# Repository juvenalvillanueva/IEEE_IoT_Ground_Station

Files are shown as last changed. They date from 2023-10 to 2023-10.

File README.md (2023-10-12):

# An IoT Ground Station: Mechanics, Control, Antenna, and Reception from a LoRa SatelliteNetwork

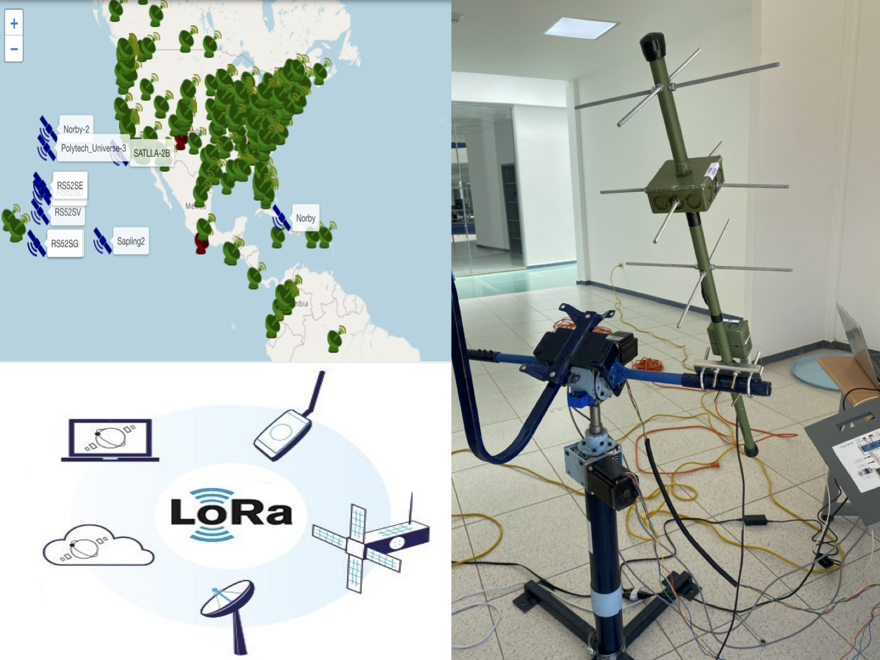
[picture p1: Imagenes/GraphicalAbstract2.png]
Graphical abstract


Se presentan los recursos y la documentación adicional obtenidos como resultado por el desarrollo del manuscrito "An IoT Ground Station: Mechanics, Control, Antenna, and Reception from a LoRa Satellite Network" publicado en IEEE Latin America Transactions. Esta información se organiza en tres carpetas: 

1. Antena, donde podrá observar los archivos del diseño y simulación de este dispositivo.

   a) El archivo Turstile.s1p es un archivo generado por un analizador vectorial redes (VNA) que contiene el parámetro S de 1 puerto (S11) medido en el laboratorio.
   
   b) El archivo turstile.nec es un archivo generado en el software libre 4NEC2 para simulación de la antena. El software puede ser descargado en:https://www.qsl.net/4nec2/.
   
2. Sistema Mecánico, aquí se encuentran los archivos de diseño y los planos para poder fabricar cada una de las piezas que conforman al sistema mecánico.
3. PID, en esta carpeta se encuentra  el código de programación del controlador PID discreto utilizado para manipular las articulaciones. Para ello, se utilizó la plataforma de Arduinoal debido a que se utilizó una placa de esta marca.

## Requerimientos
 
- Sistema operativo Windows.
- Microsoft Excel.
- Matlab 2018 o posteriores con el “RF Toolbox” instalado.
- Última versión de 4NEC2.
- SolidWorks 2018 o posteriores.
- Plataforma de Arduino.

## Imagenes

<div id="header" align="center">
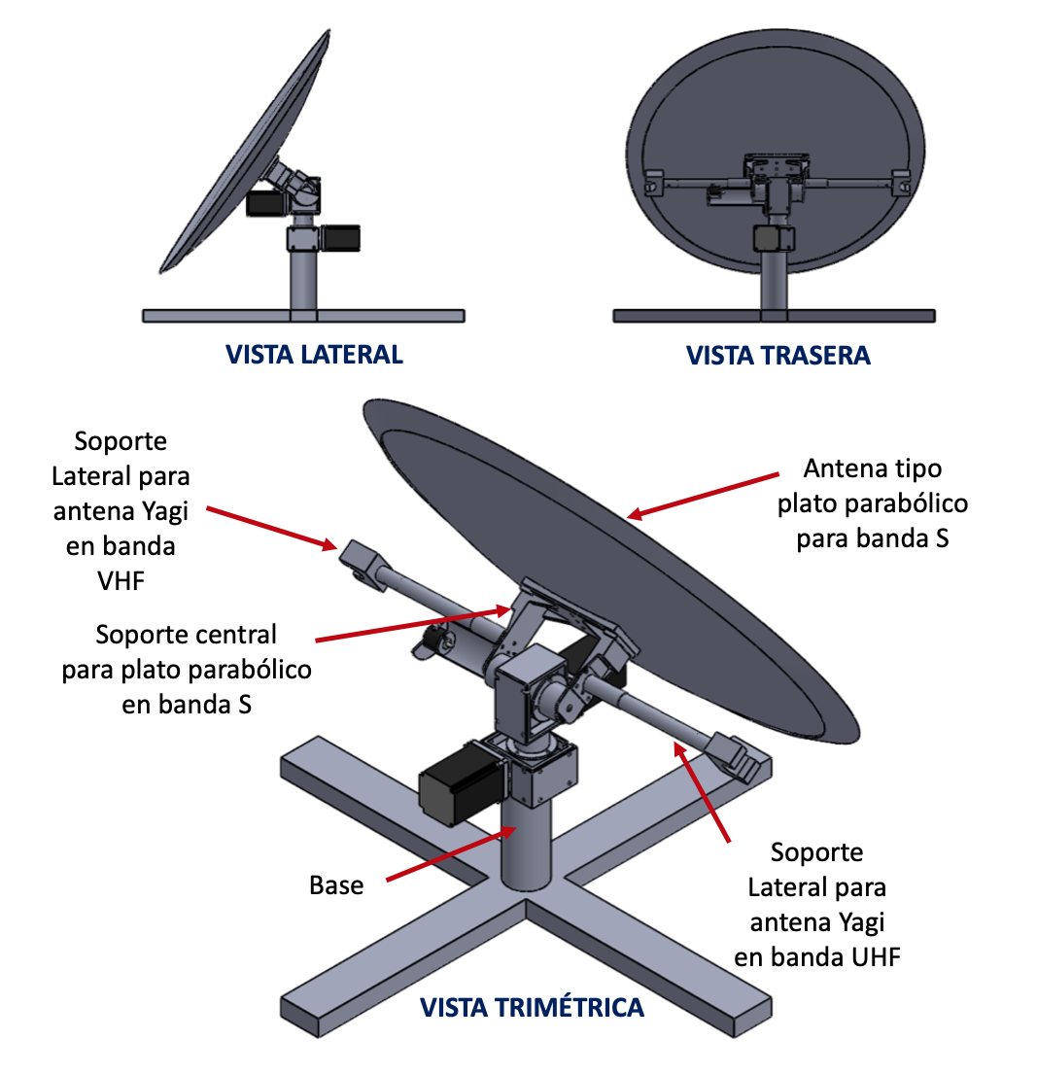
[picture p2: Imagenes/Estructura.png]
  
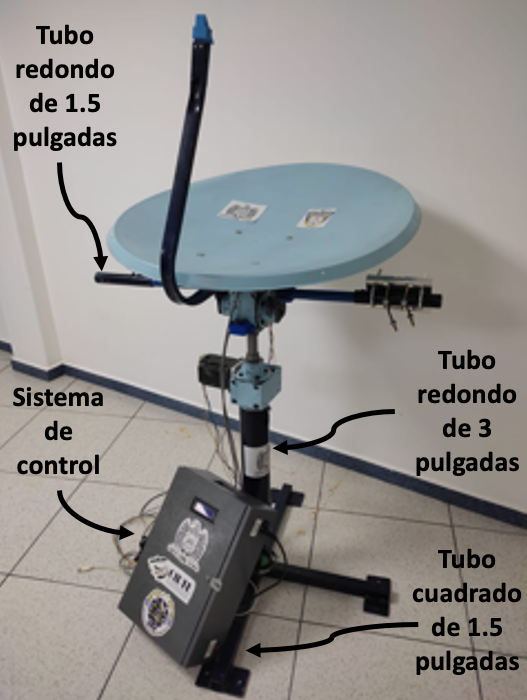
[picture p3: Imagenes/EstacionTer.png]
  
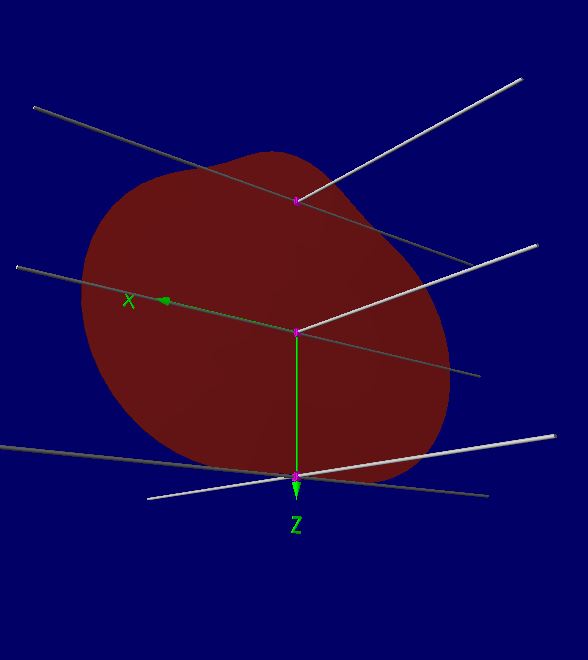
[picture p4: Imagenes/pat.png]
  
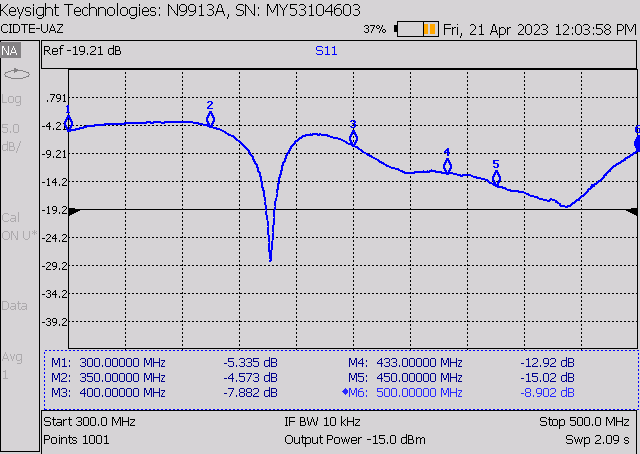
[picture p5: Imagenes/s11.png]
  
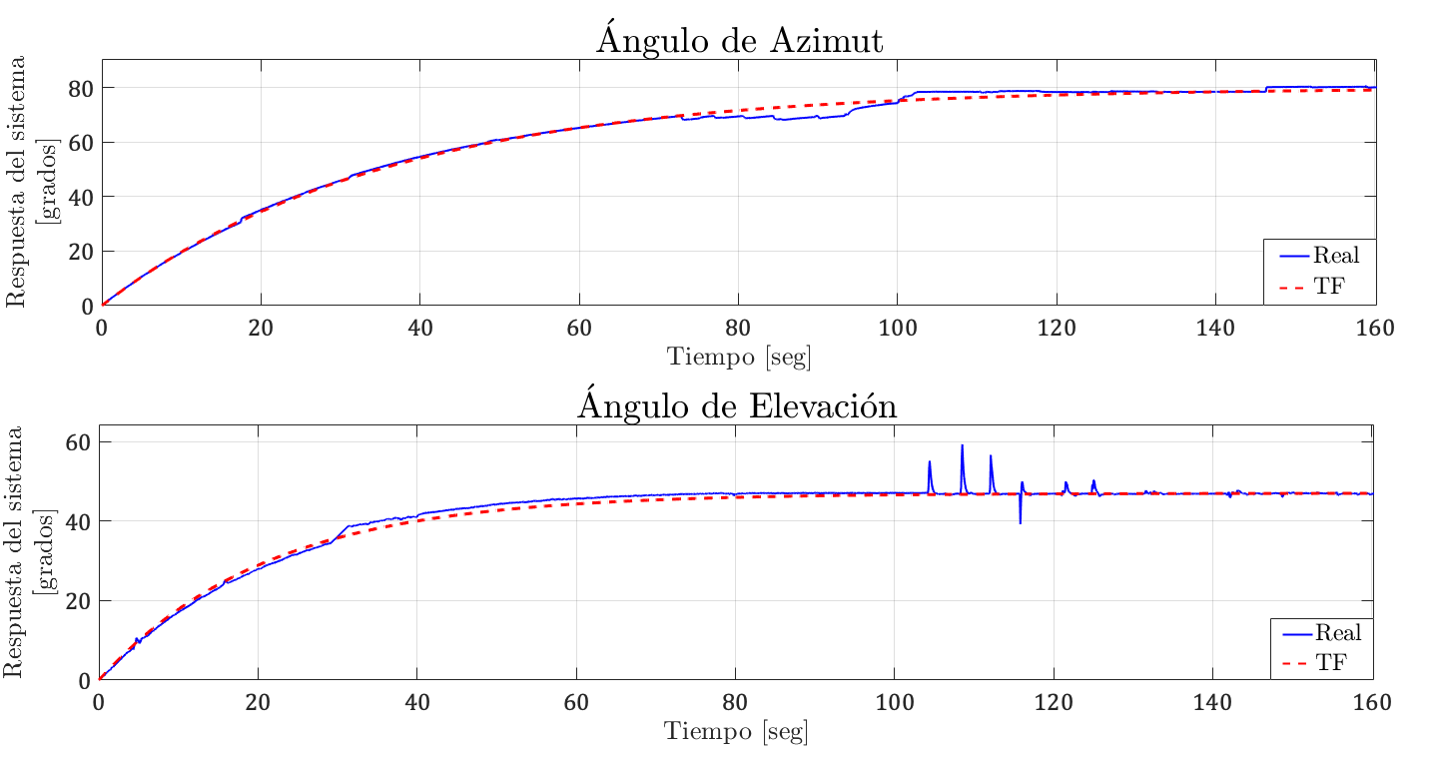
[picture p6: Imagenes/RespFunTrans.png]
 
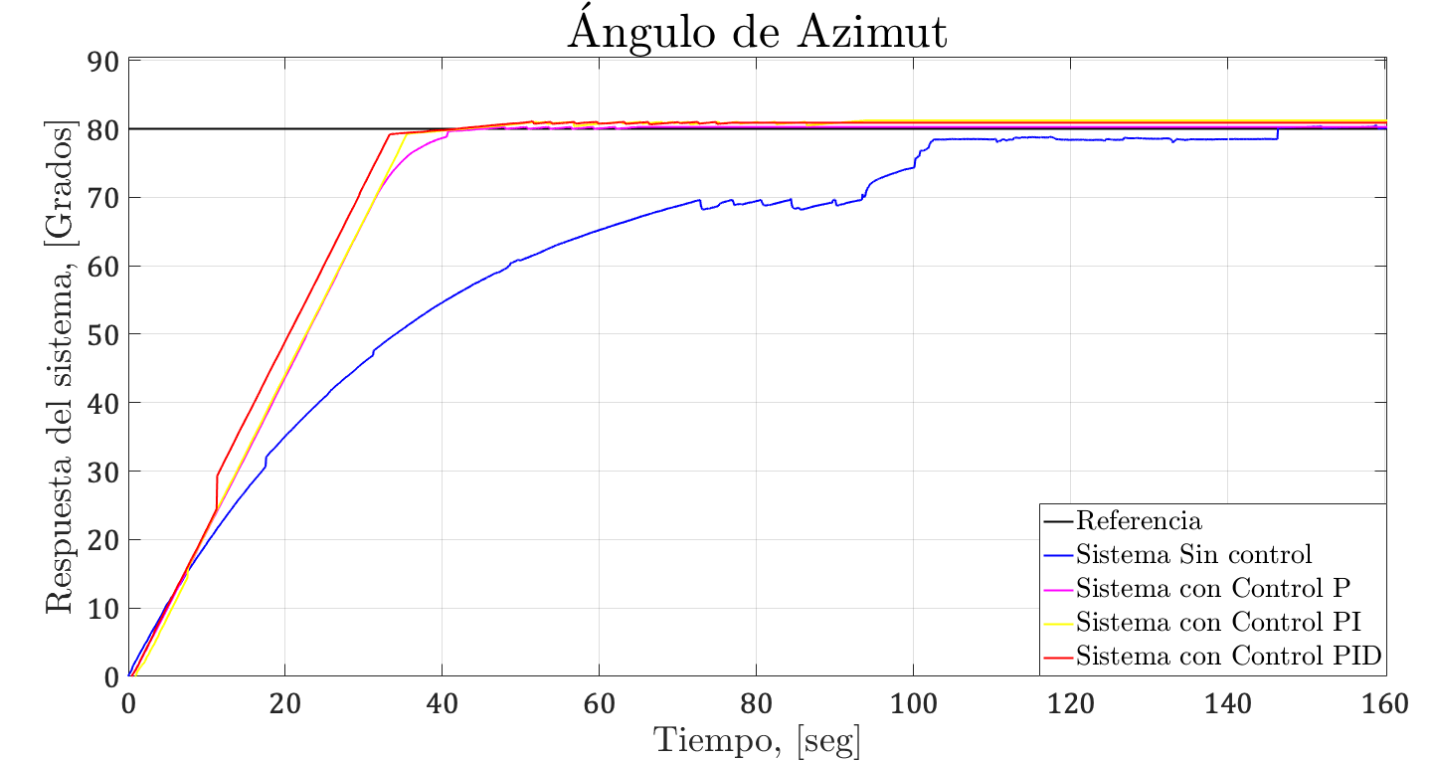
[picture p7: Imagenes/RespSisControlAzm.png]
  
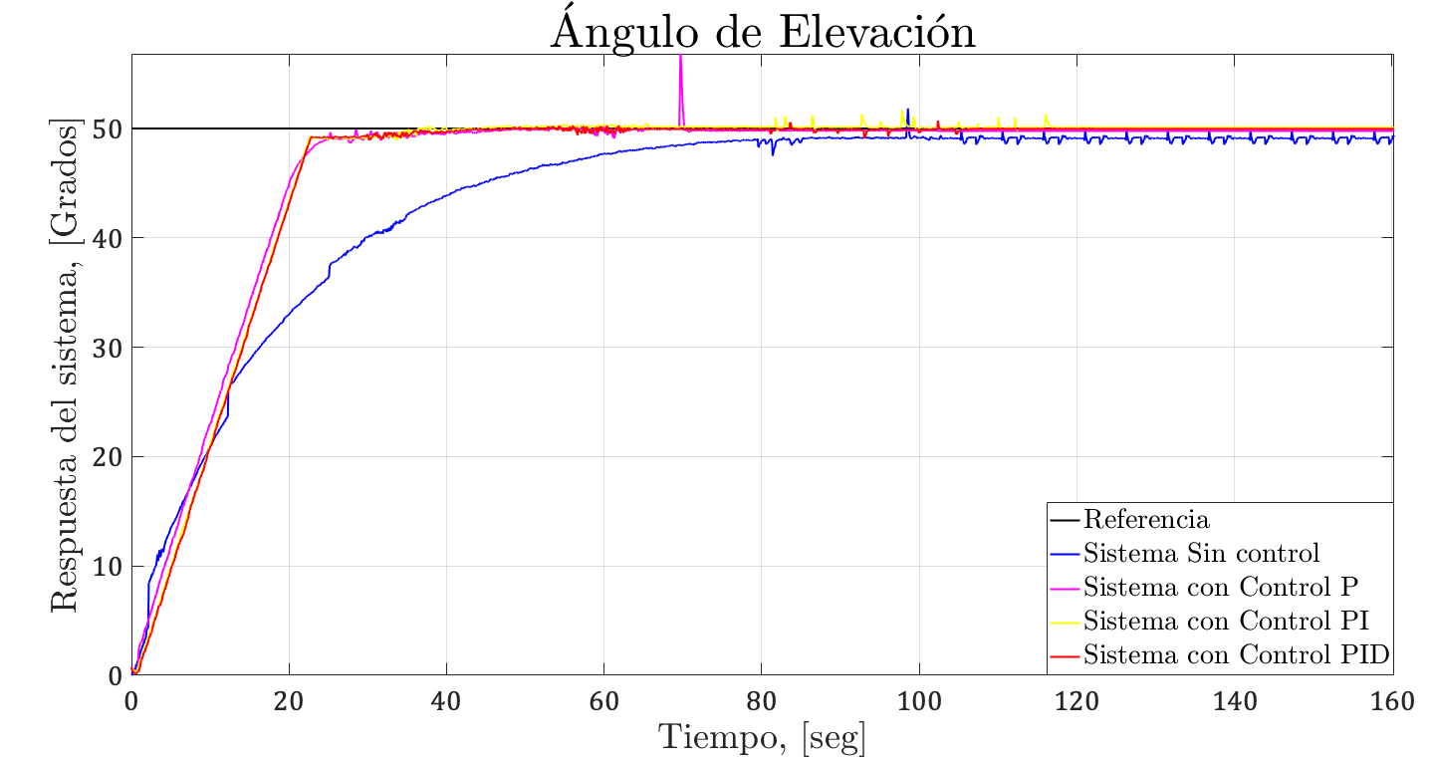
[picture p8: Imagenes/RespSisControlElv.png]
  
</div>

## Instrucciones

1.a) Las mediciones incluidas en el archivo Turstile.s1p pueden ser visualizadas con solo arrástralo a una nueva hoja de Excel. Ya en Excel se pueden observar tres columnas correspondientes al barrido de frecuencia, la magnitud del parámetro S11 (coeficiente de reflexión en dB) y su fase. Con ello se pueden obtener graficas tanto de magnitud y fase de S11 vs frecuencia. Las mediciones contenidas en el archivo archivo puede ser también observadas en alguna reciente versión de Matlab con el de “RF Toolbox” instalado. Se escribe un m-file en el “Editor” para graficar el parámetro S11 en dB de la siguiente forma:

S=sparameters(“Turnstile.s1p”);
rfplot(S)

Si desean graficar otros parámetros de la antena como carta de Smith, VWR o impedancia, cheque la ayuda con en la ventana “Comand Window” tecleando:

help rfplot

1.b) El archivo turstile.nec se abre en la venta “Main” en la opción “Open 4NEC2 in/out file”. Este archivo ya hecho a modo para la antena utilizada permite observar los parámetros de antena simulados como los dependientes de la frecuencia como S11 en dB, VWR, impedancia, etc. Para más información del uso de 4NEC2, vea los siguientes videos en YouTube:

- https://www.youtube.com/watch?v=vaLx3_F6-b4
- https://www.youtube.com/watch?v=T5hyCiytaFk

2. Se comparten los archivos de los planos en formato PDF de manera que puedan utilizarlos para fabricar y reproducir cada una de las piezas mecánicas. Así también, los archivos en formato SLDPRT los cuales pueden abrir mediante SOLIDWORKS para que puedan realizar los cambios en el diseño conforme a sus requerimientos.
3. Para el control de las articulaciones, se utilizó una tarjeta de tipo ARDUINO, por lo que, el archivo del código del controlador PID esta en etse formato.

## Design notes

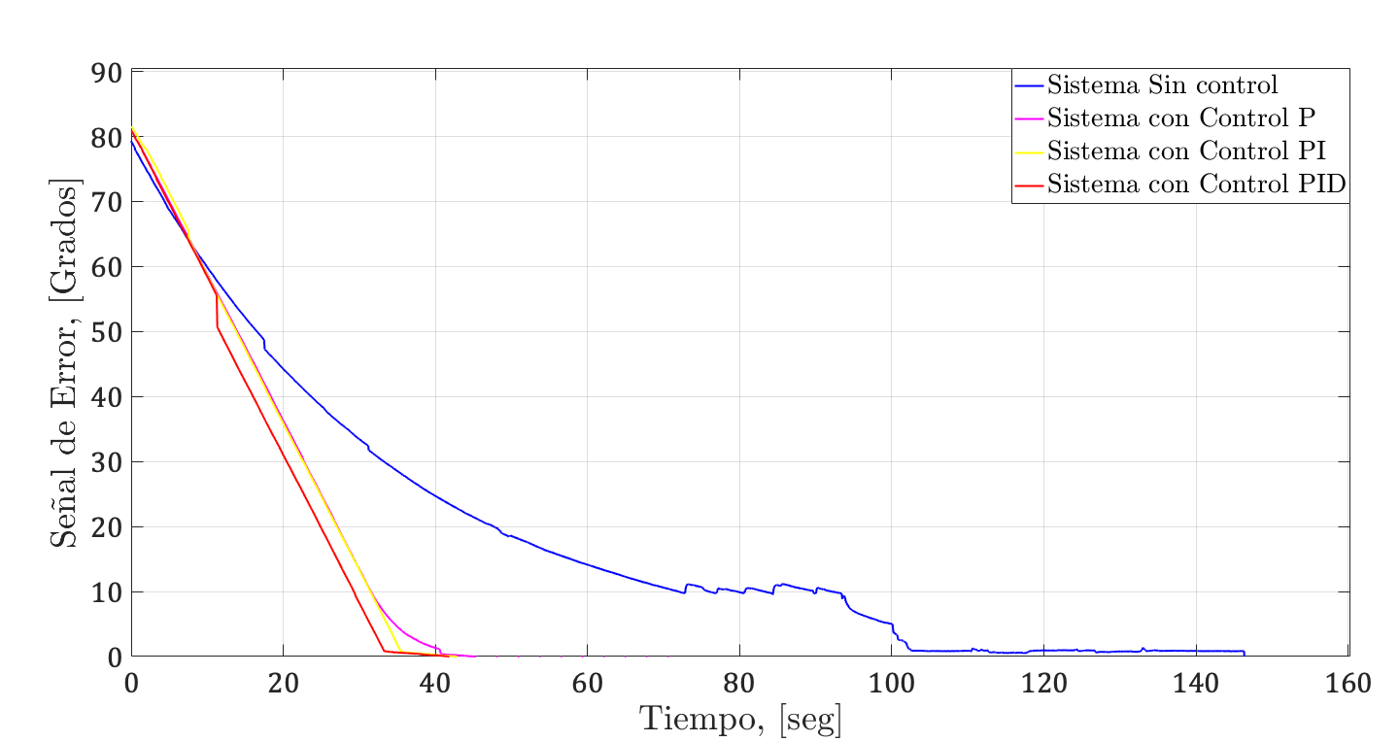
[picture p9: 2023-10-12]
Imagenes/E(t)Azm.png

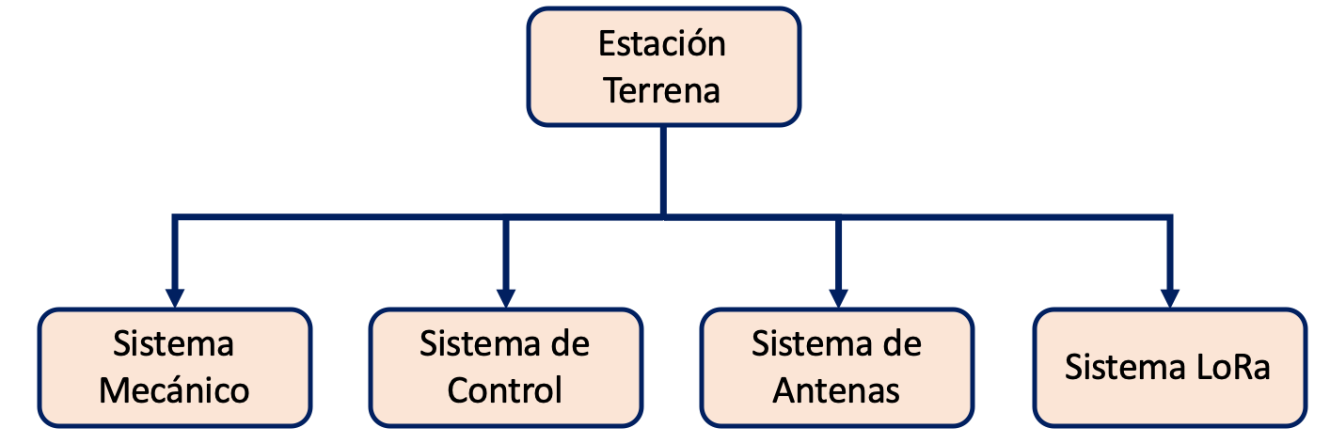
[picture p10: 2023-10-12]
Imagenes/Metodologia.png

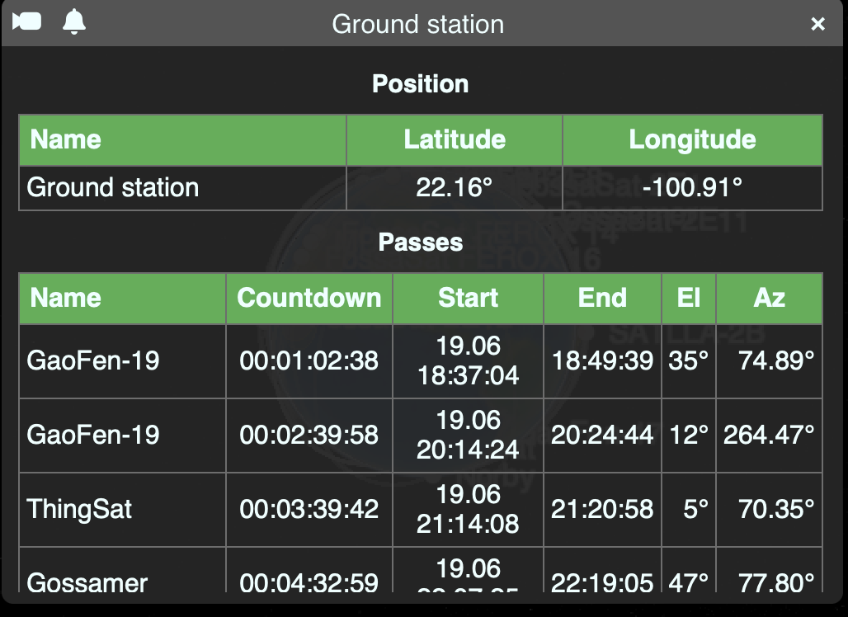
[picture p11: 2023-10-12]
Imagenes/coordenadas.png

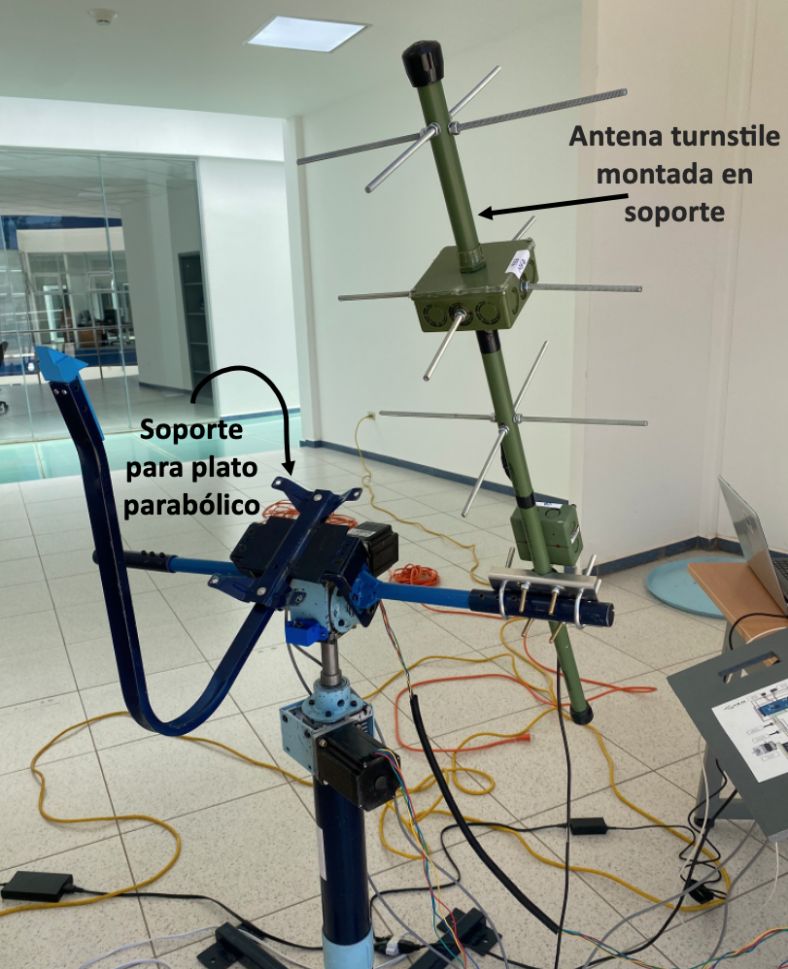
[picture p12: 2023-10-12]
Imagenes/antena.png

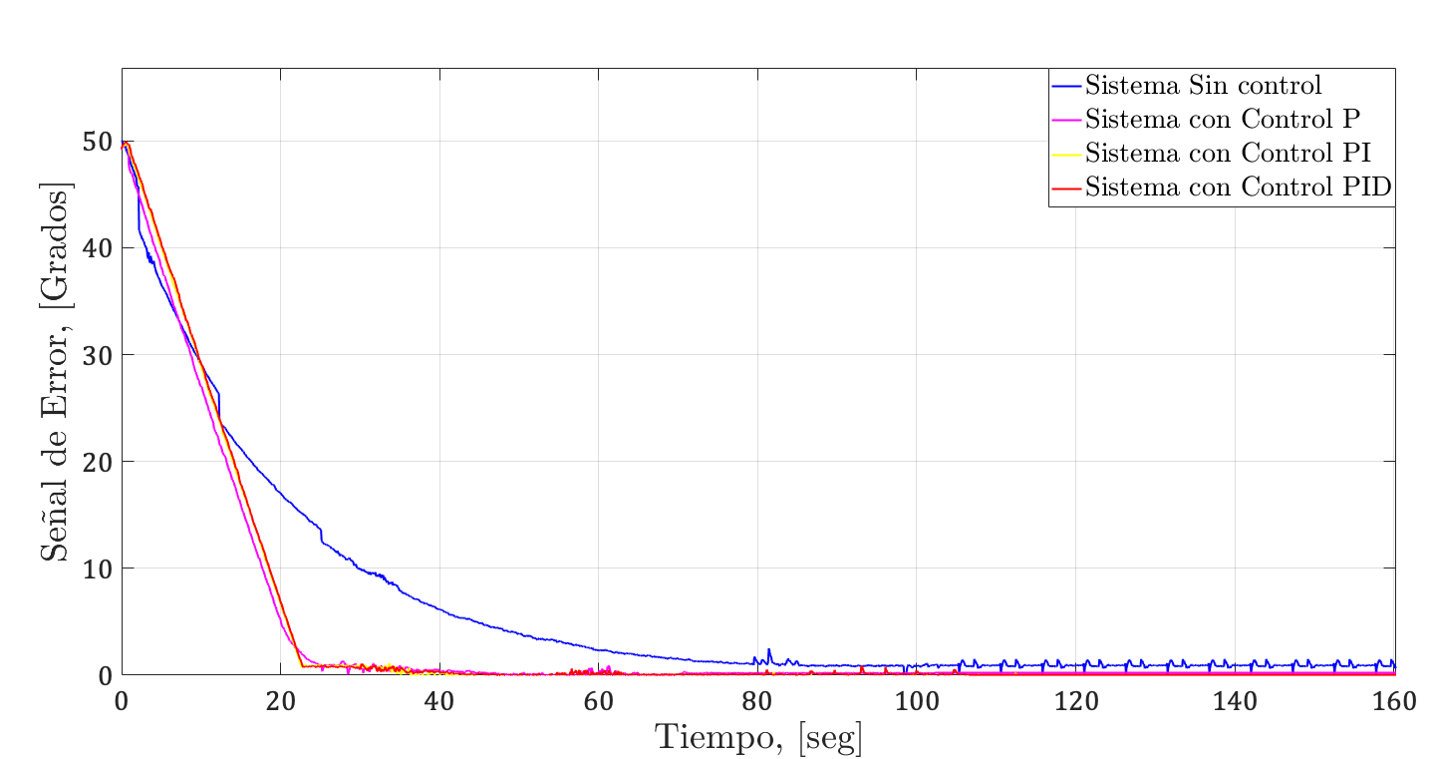
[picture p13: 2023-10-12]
Imagenes/E(t)Elv.png

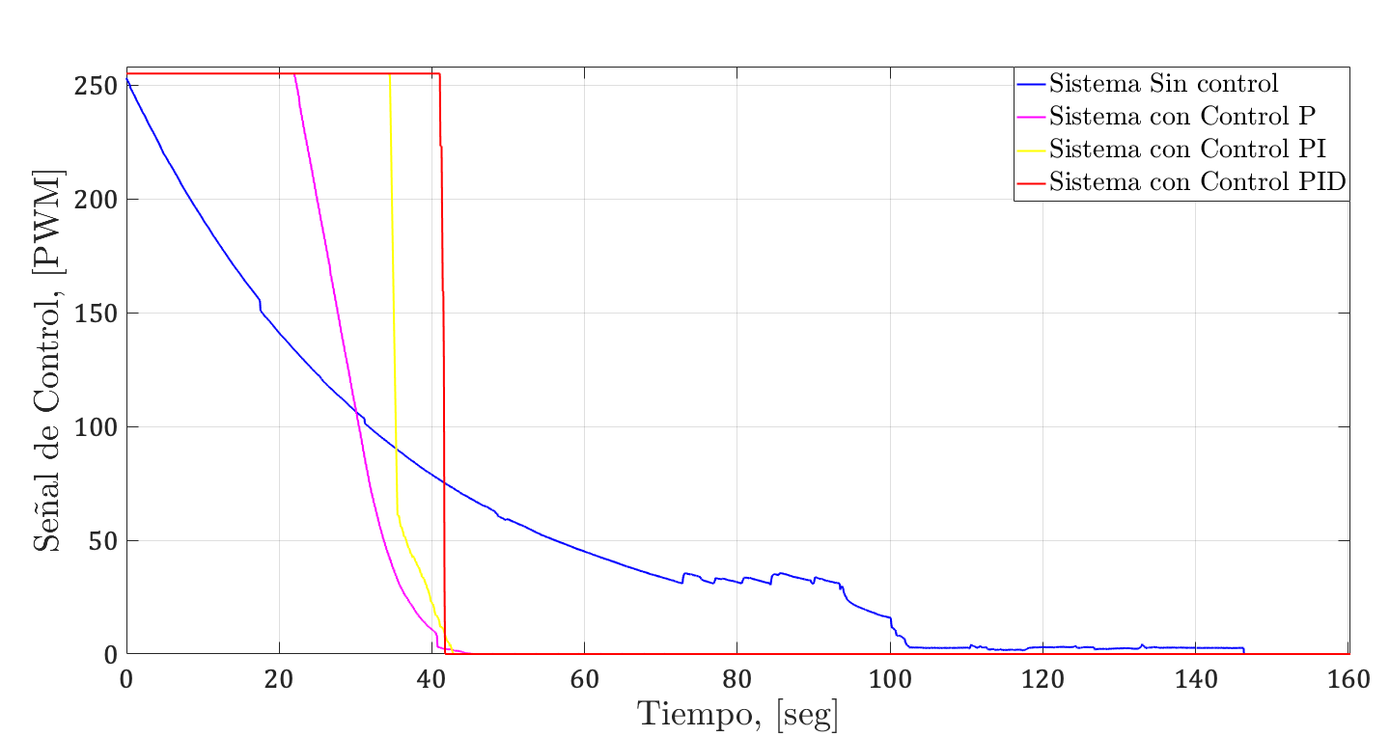
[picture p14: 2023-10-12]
Imagenes/U(t)Azm.png

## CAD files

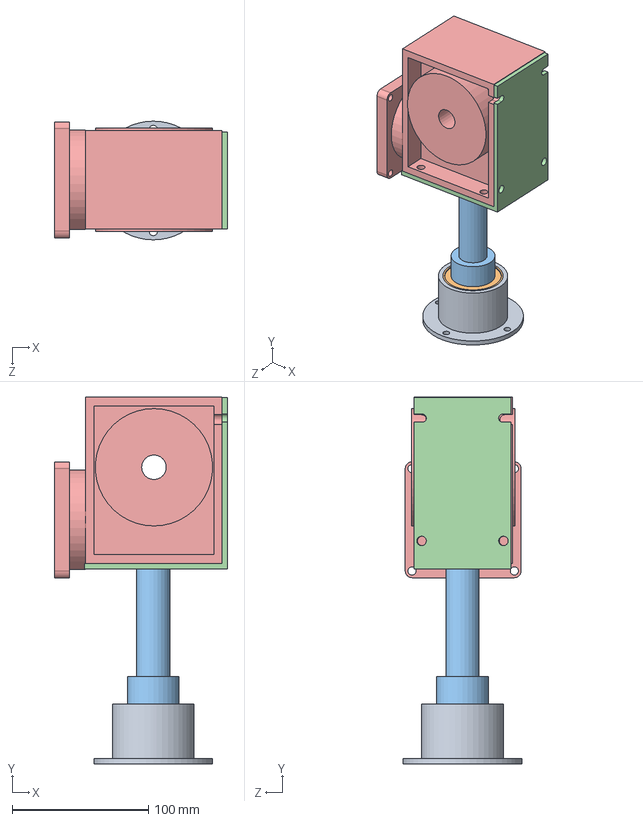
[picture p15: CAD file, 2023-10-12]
Sistema_Mecánico/Diseño/Ensamblaje_4_SoporteBrocheNMRV40.SLDASM
127.0 x 269.0 x 87.0 mm
Pieza_5_SoporteEjeReductor_NMRV40
Pieza_6_Balero52mm
Pieza_7_BrocheEje_NMRV40
Pieza_4_SoporteReductor_NMRV40
Pieza_1_Reductor_NMRV40

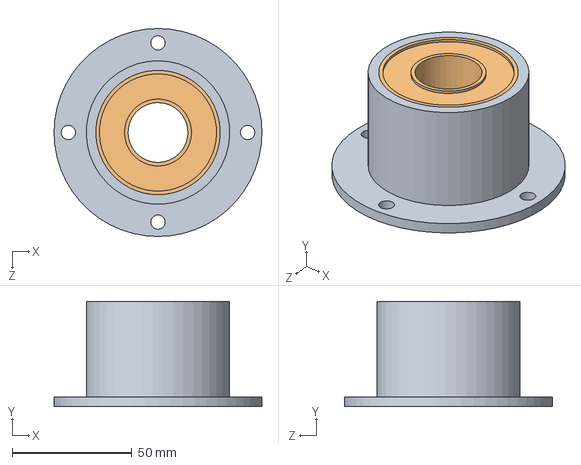
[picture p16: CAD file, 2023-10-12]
Sistema_Mecánico/Diseño/Ensamblaje_2_SoporteNMRV40_Balero52mm.SLDASM
87.0 x 44.0 x 87.0 mm
Pieza_5_SoporteEjeReductor_NMRV40
Pieza_6_Balero52mm

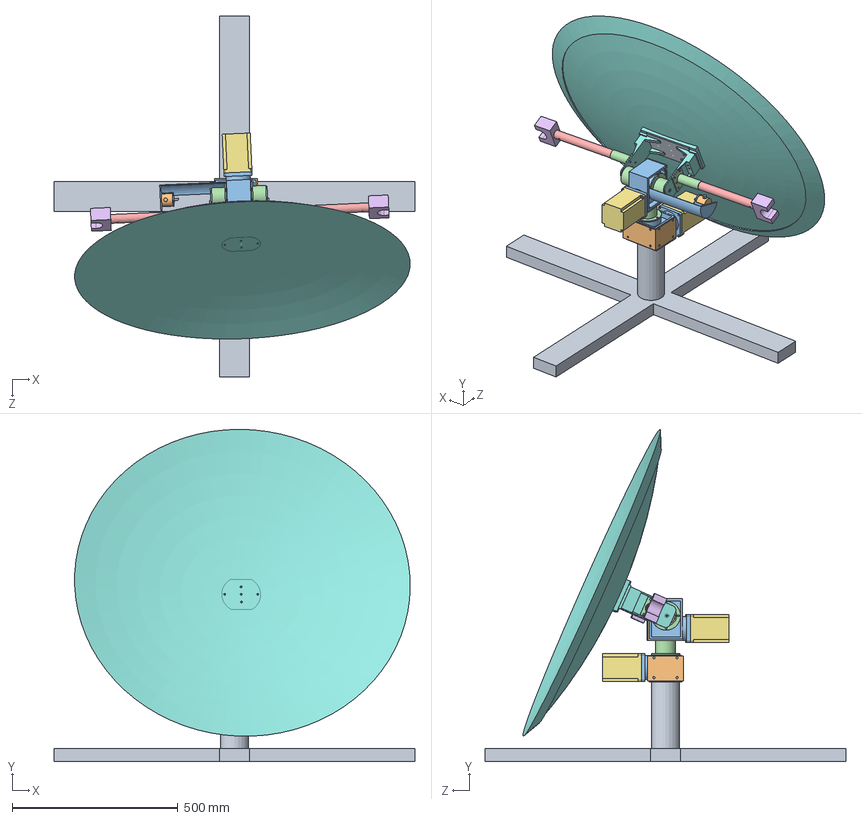
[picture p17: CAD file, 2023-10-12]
Sistema_Mecánico/Diseño/Ensamblaje_5_EstacionTerrena.SLDASM
1090.0 x 1003.2 x 1090.0 mm
Pieza_2_Base
Pieza_12_CajaReductorNMRV40
Pieza_1_Reductor_NMRV40 x 2
Pieza_5_SoporteEjeReductor_NMRV40 x 3
Pieza_6_Balero52mm x 3
Pieza_7_BrocheEje_NMRV40
Pieza_4_SoporteReductor_NMRV40
Pieza_8_SoporteBase x 2
Pieza_9_PlacaBase
Pieza_13_Encoder x 2
Pieza_5_SoporteEjeReductor_NMRV40_v2
Pieza_14 x 2
Pieza_15_BrazoAntena x 2
Pieza_16_BrocheAntena x 2
Pieza_17_MotorHB x 2
Pieza_20_Antena

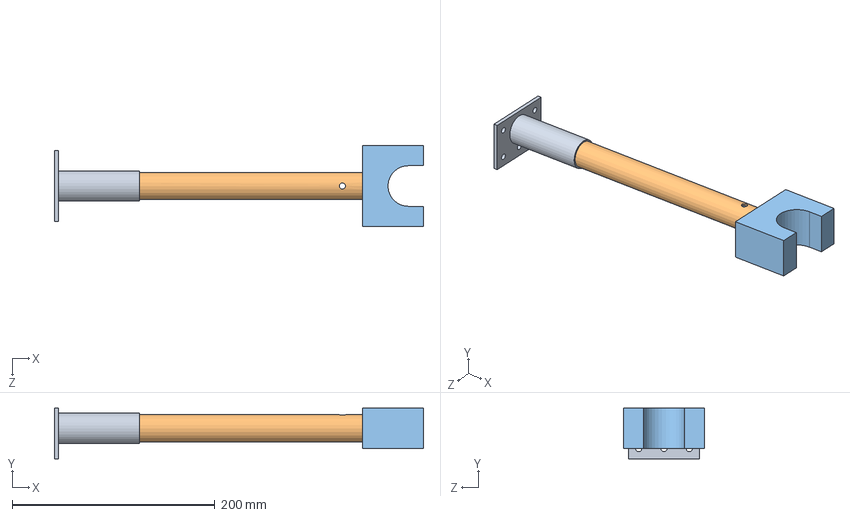
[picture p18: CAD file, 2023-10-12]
Sistema_Mecánico/Diseño/Ensamblaje_6_BrazoEstacion.SLDASM
364.0 x 50.0 x 80.0 mm
Pieza_14
Pieza_15_BrazoAntena
Pieza_16_BrocheAntena

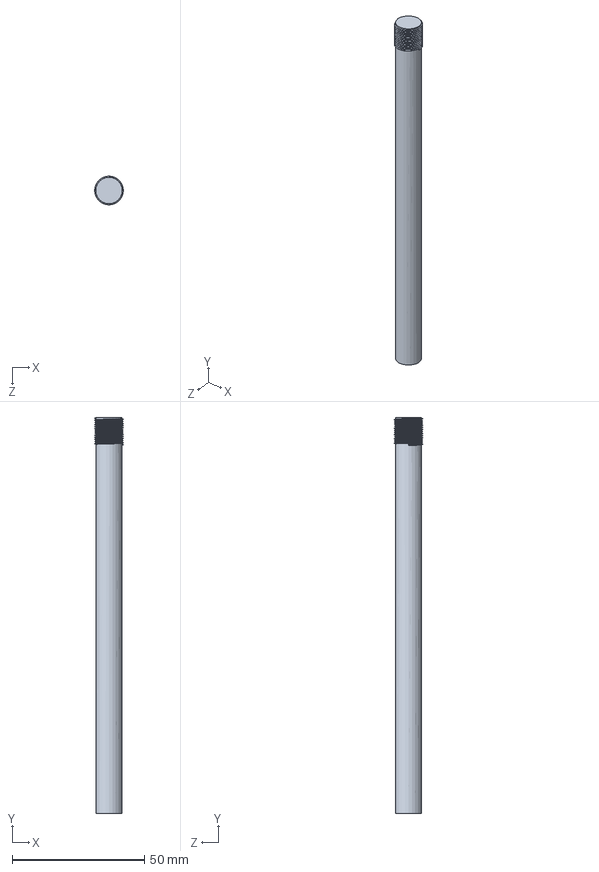
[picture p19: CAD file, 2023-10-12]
Sistema_Mecánico/Diseño/Pieza_11_EjeConectorEncoder.SLDPRT
10.9 x 150.0 x 10.9 mm

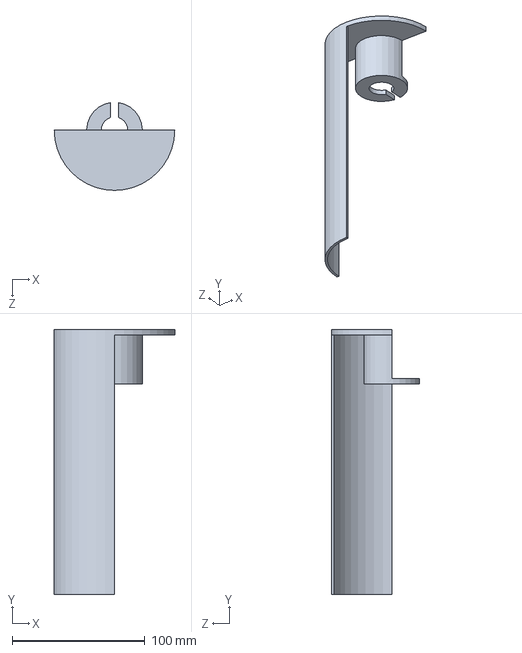
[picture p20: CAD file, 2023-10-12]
Sistema_Mecánico/Diseño/Pieza_5_SoporteEjeReductor_NMRV40_v2.SLDPRT
91.0 x 200.0 x 66.3 mm

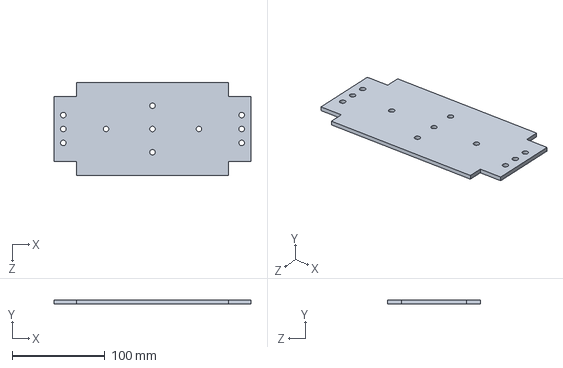
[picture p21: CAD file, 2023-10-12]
Sistema_Mecánico/Diseño/Pieza_9_PlacaBase.SLDPRT
212.0 x 4.00 x 100.0 mm

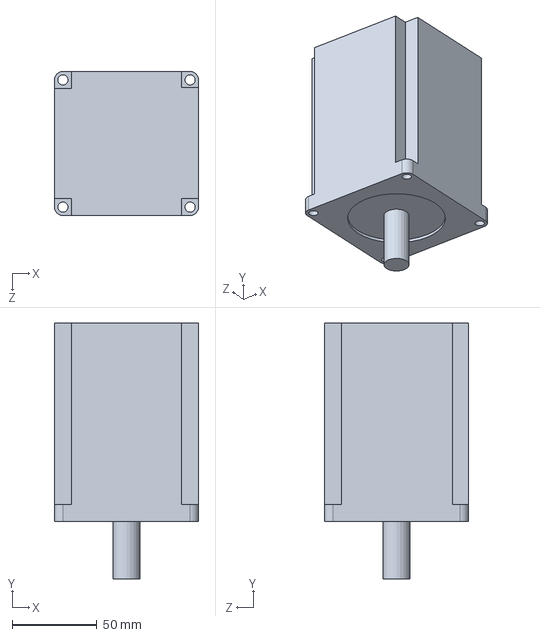
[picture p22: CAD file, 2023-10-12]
Sistema_Mecánico/Diseño/Pieza_17_MotorHB.SLDPRT
85.0 x 151.0 x 85.0 mm

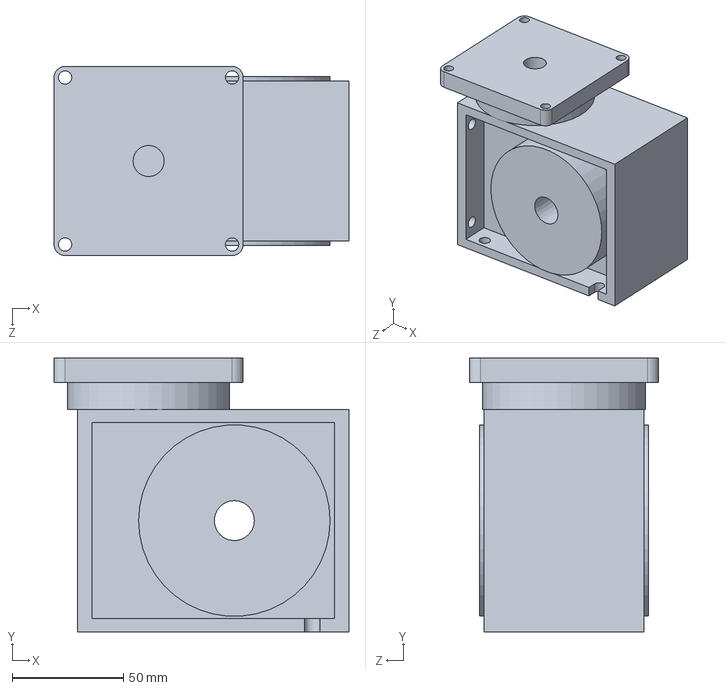
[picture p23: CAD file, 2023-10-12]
Sistema_Mecánico/Diseño/Pieza_1_Reductor_NMRV40.SLDPRT
132.5 x 123.0 x 85.0 mm

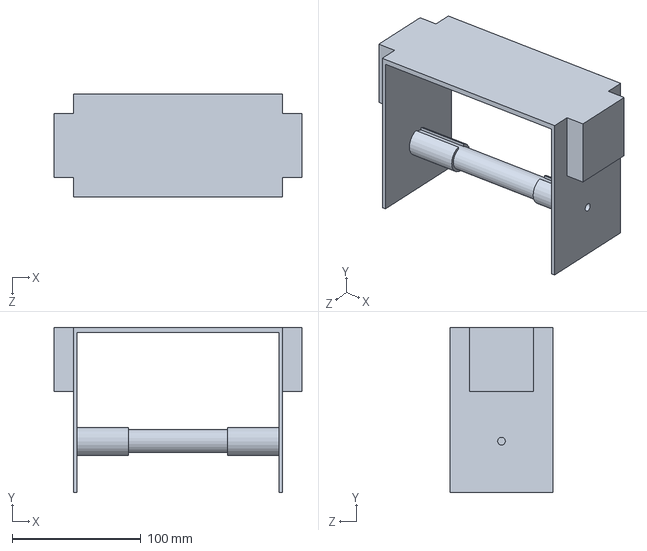
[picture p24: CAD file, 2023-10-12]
Sistema_Mecánico/Diseño/Pieza_3_SoporteAntena.SLDPRT
193.0 x 128.5 x 80.0 mm

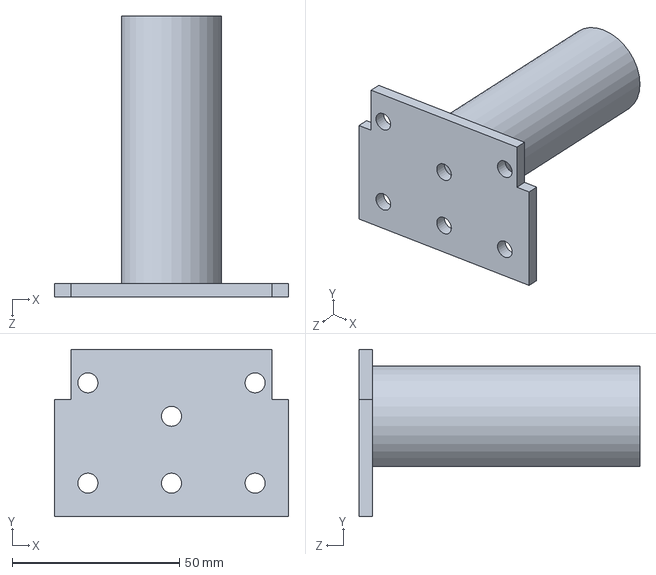
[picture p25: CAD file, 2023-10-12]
Sistema_Mecánico/Diseño/Pieza_14.SLDPRT
70.0 x 50.0 x 84.0 mm

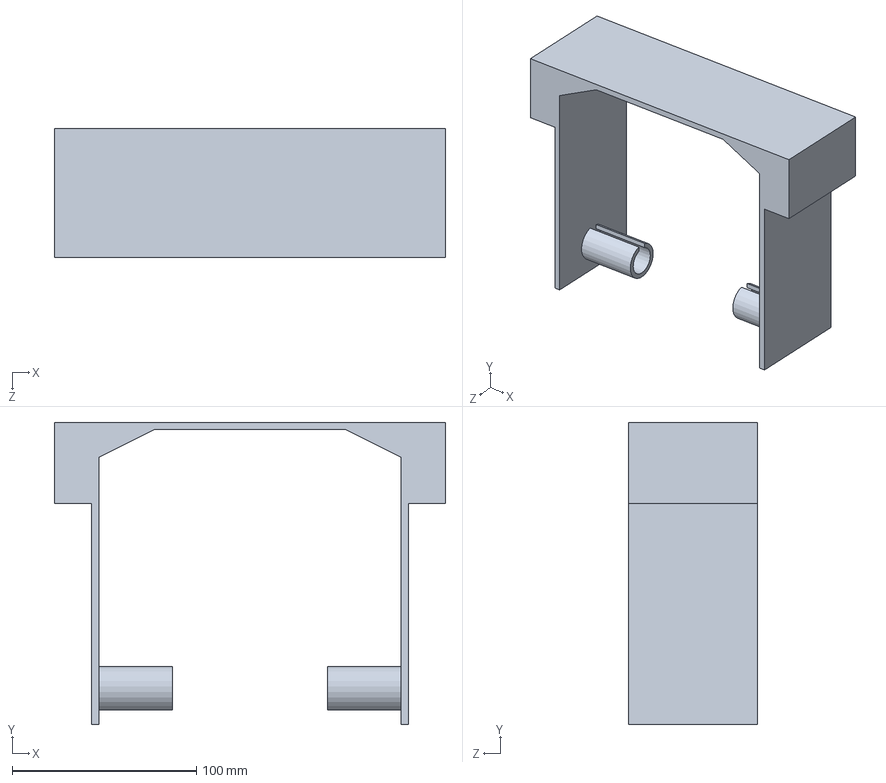
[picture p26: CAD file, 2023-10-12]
Sistema_Mecánico/Diseño/Pieza_10_SoporteAntena_V2.SLDPRT
212.0 x 164.0 x 70.0 mm

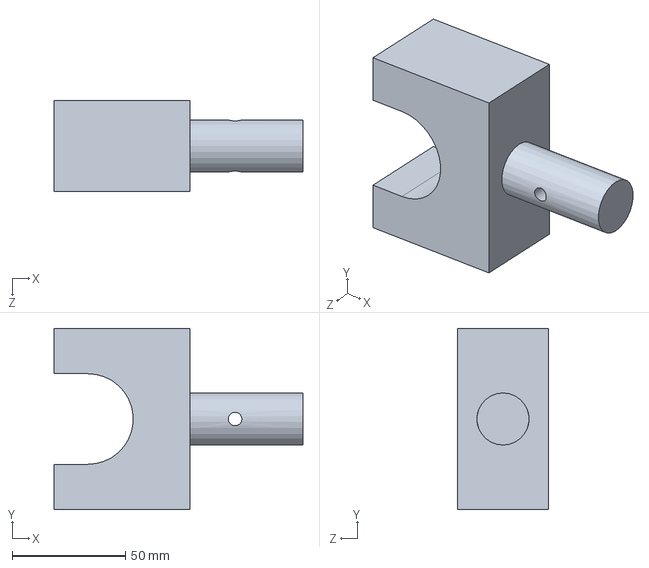
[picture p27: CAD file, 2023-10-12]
Sistema_Mecánico/Diseño/Pieza_16_BrocheAntena.SLDPRT
110.0 x 80.0 x 40.0 mm

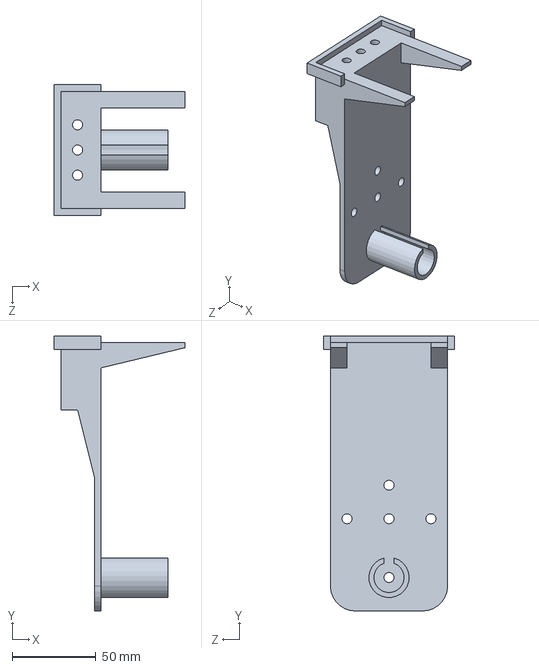
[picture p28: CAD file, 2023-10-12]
Sistema_Mecánico/Diseño/Pieza_8_SoporteBase.SLDPRT
78.0 x 164.0 x 78.0 mm

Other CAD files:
Sistema_Mecánico/Diseño/Pieza_5_SoporteEjeReductor_NMRV40.SLDPRT
Sistema_Mecánico/Diseño/Pieza_13_Encoder.SLDPRT
Sistema_Mecánico/Diseño/Pieza_7_BrocheEje_NMRV40.SLDPRT
Sistema_Mecánico/Diseño/Pieza_4_SoporteReductor_NMRV40.SLDPRT
Sistema_Mecánico/Diseño/Pieza_12_CajaReductorNMRV40.SLDPRT
Sistema_Mecánico/Diseño/Pieza_15_BrazoAntena.SLDPRT
Sistema_Mecánico/Diseño/Pieza_20_Antena.SLDPRT
Sistema_Mecánico/Diseño/Pieza_2_Base.SLDPRT
Sistema_Mecánico/Diseño/Pieza_6_Balero52mm.SLDPRT
Sistema_Mecánico/Diseño/Pieza_8_SoporteBase_Construccion_2.SLDDRW
Sistema_Mecánico/Planos/Archivos SLDDRW/Plano_12_CajaReductorNMRV40.SLDDRW
Sistema_Mecánico/Planos/Archivos SLDDRW/Plano_4_SoporteReductor_NMRV40.SLDDRW
Sistema_Mecánico/Planos/Archivos SLDDRW/Plano_5_EstacionTerrena.SLDDRW
Sistema_Mecánico/Planos/Archivos SLDDRW/Plano_5_SoporteEjeReductor_NMRV40.SLDDRW
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

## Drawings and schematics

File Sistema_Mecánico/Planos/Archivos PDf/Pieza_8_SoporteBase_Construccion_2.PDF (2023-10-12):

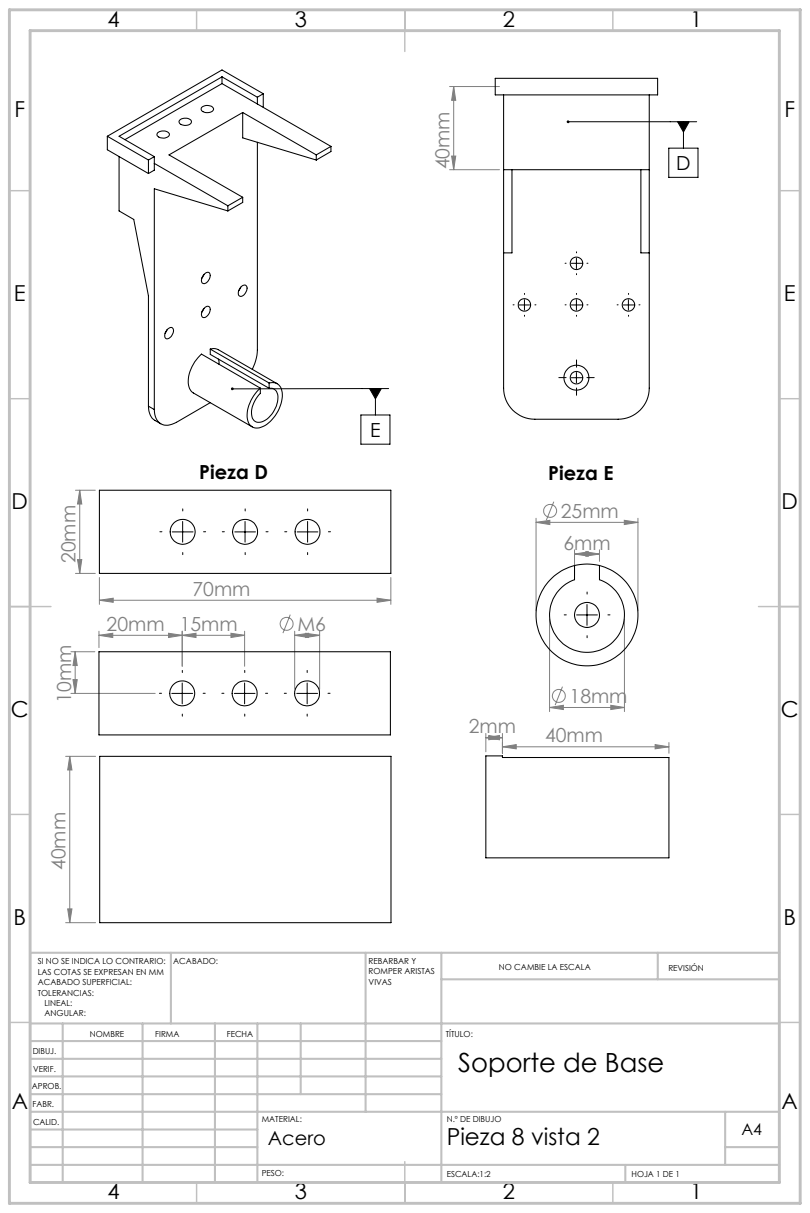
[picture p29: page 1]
Pieza D; Pieza E; ACABADO:; REBARBAR Y; ROMPER ARISTAS; NO CAMBIE LA ESCALA; REVISIÓN; ESCALA:1:2; HOJA 1 DE 1

SI NO SE INDICA LO CONTRARIO:
LAS COTAS SE EXPRESAN EN MM
ACABADO SUPERFICIAL:
TOLERANCIAS:
LINEAL:
ANGULAR:

NOMBRE | FIRMA | FECHA | | | | TÍTULO: Soporte de Base

DIBUJ.
VERIF.
APROB.
FABR.
CALID. | | | | MATERIAL: Acero | N.º DE DIBUJO Pieza 8 vista 2 | A4

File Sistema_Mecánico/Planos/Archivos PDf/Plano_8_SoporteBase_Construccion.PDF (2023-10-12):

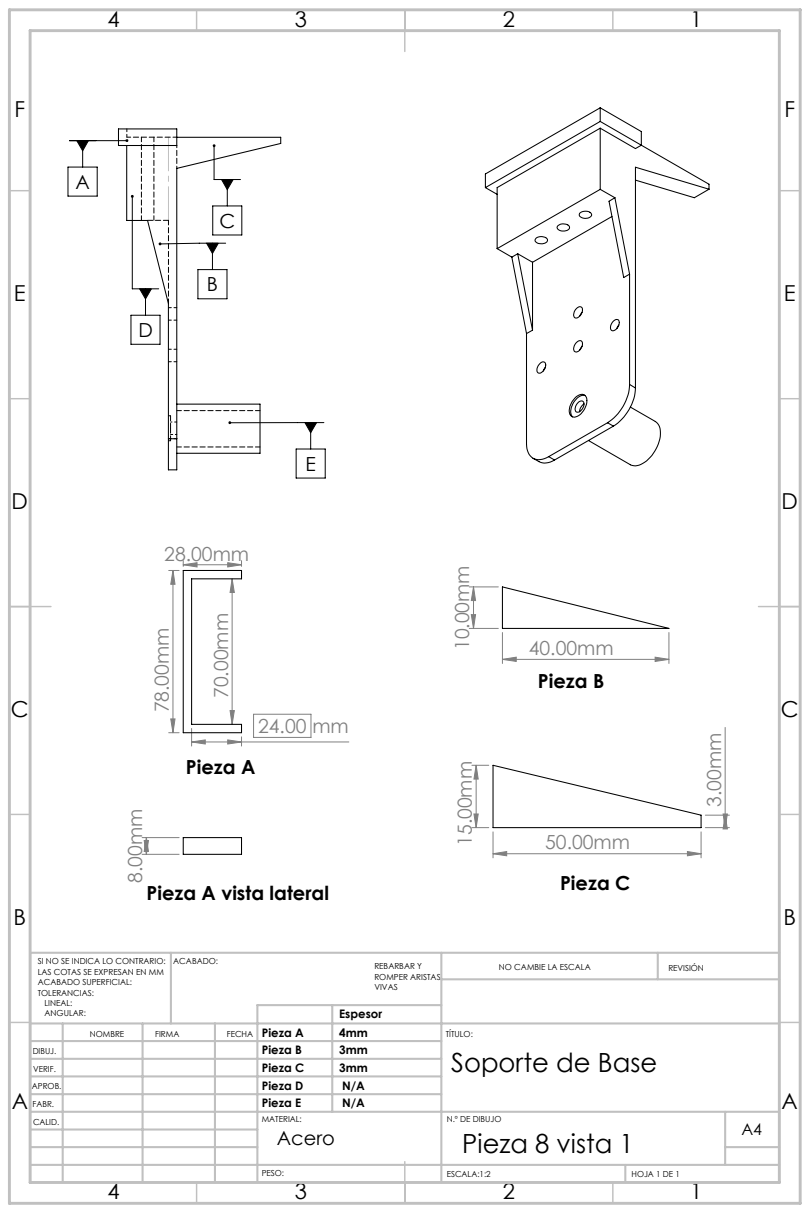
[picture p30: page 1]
Pieza A; Pieza B; Pieza C; ACABADO:; REBARBAR Y; ROMPER ARISTAS; NO CAMBIE LA ESCALA; REVISIÓN; ESCALA:1:2; HOJA 1 DE 1

8.00mm Pieza A vista lateral

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

Espesor

NOMBRE | FIRMA | FECHA | Pieza A | 4mm | TÍTULO: Soporte de Base

DIBUJ. | | | | Pieza B | 3mm
VERIF. | | | | Pieza C | 3mm
APROB. | | | | Pieza D | N/A
FABR. | | | | Pieza E | N/A
CALID. | | | | MATERIAL: Acero | N.º DE DIBUJO Pieza 8 vista 1 | A4

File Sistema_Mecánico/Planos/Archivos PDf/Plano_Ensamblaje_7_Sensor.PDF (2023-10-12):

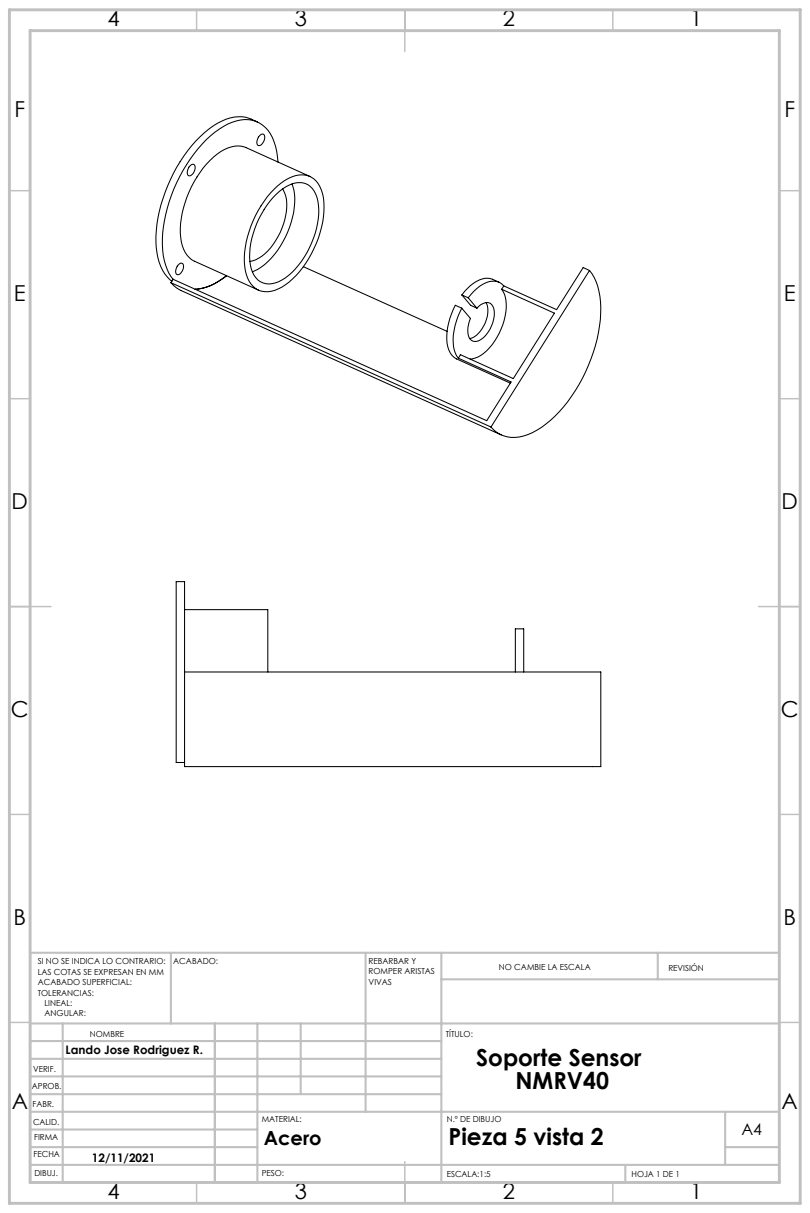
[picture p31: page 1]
ACABADO:; REBARBAR Y; ROMPER ARISTAS; NO CAMBIE LA ESCALA; REVISIÓN

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

NOMBRE | | | | | TÍTULO: Soporte Sensor NMRV40
Lando Jose Rodriguez R.

VERIF.
APROB.
FABR.
CALID. | | | MATERIAL: Acero | N.º DE DIBUJO Pieza 5 vista 2 | A4
FIRMA
FECHA | 12/11/2021
DIBUJ. | | | PESO: | | ESCALA:1:5 | HOJA 1 DE 1

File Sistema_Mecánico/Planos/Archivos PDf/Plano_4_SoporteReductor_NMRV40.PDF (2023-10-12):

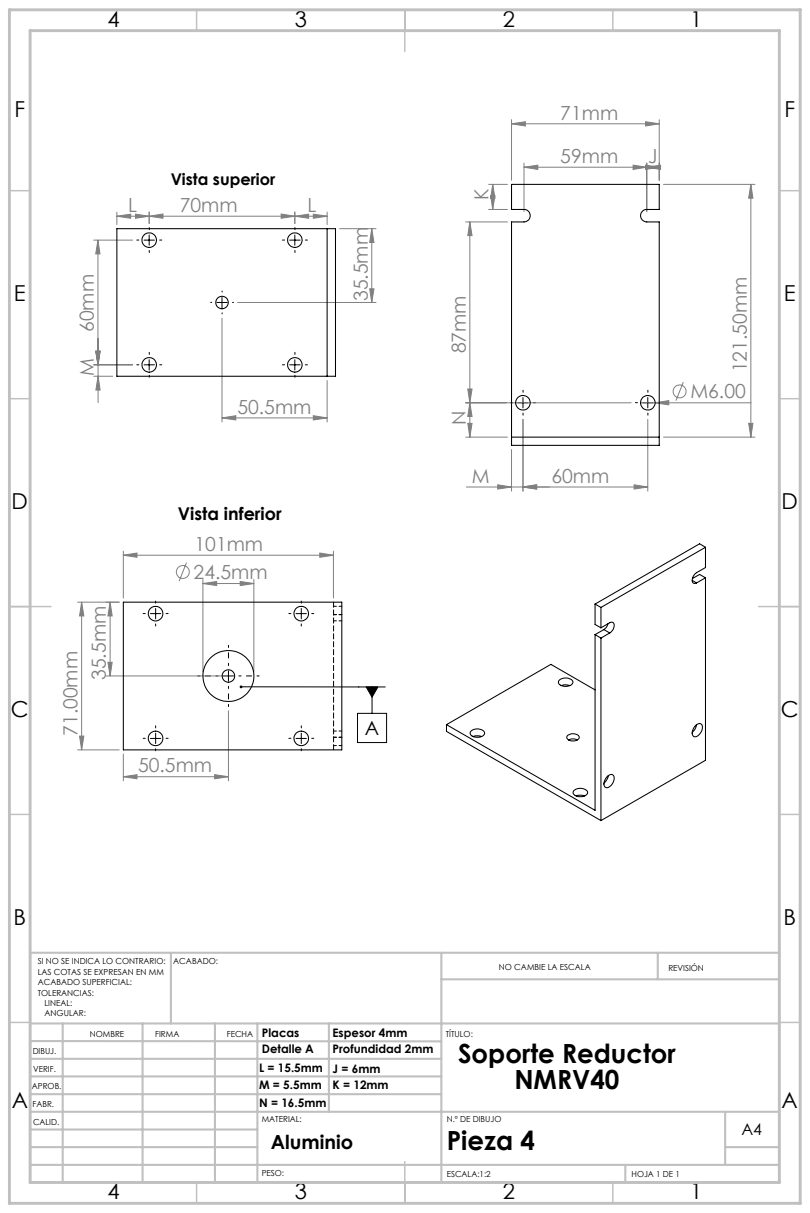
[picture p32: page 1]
Vista superior; Vista inferior; NO CAMBIE LA ESCALA; REVISIÓN; ESCALA:1:2; HOJA 1 DE 1

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

NOMBRE | FIRMA | FECHA | Placas | Espesor 4mm | TÍTULO: Soporte Reductor NMRV40

DIBUJ. | | | | Detalle A | Profundidad 2mm
VERIF. | | | | L = 15.5mm | J = 6mm
APROB. | | | | M = 5.5mm | K = 12mm
FABR. | | | | N = 16.5mm
CALID. | | | | MATERIAL: Aluminio | N.º DE DIBUJO Pieza 4 | A4

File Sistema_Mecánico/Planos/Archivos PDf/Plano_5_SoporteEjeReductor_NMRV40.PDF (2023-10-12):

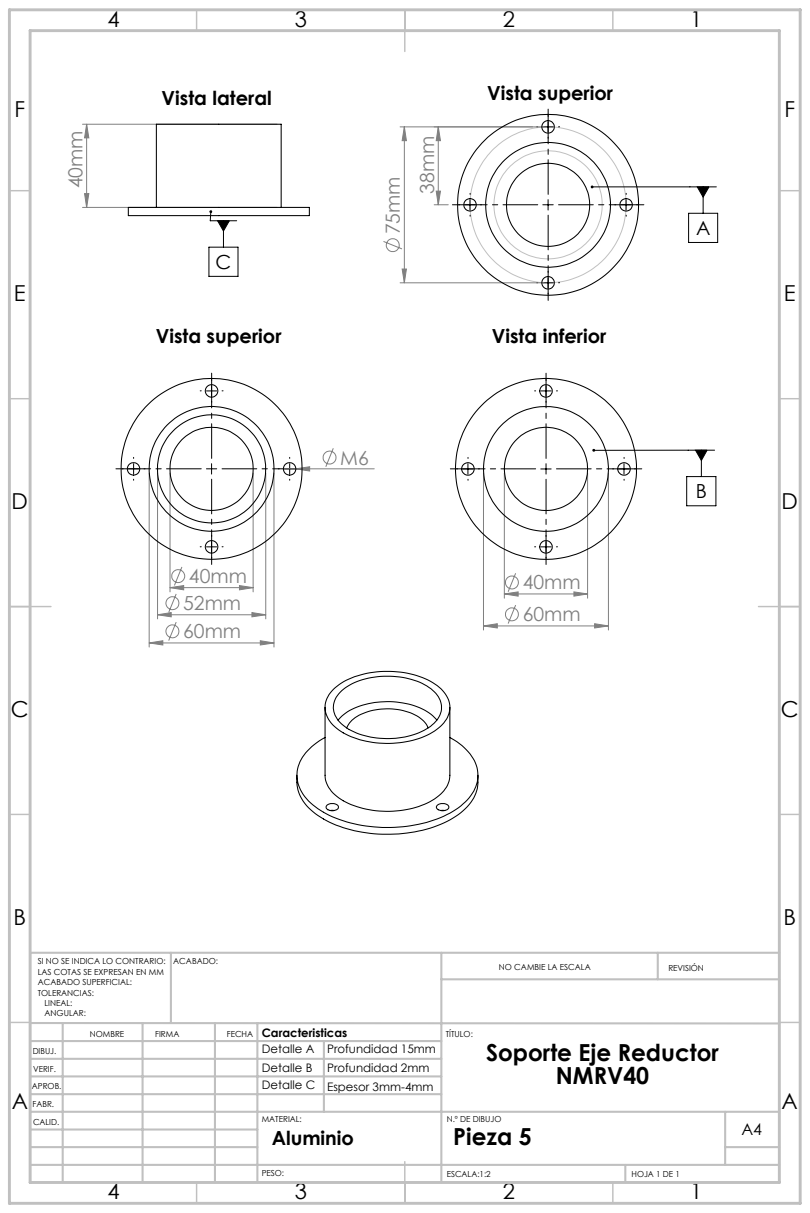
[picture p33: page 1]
Vista lateral; Vista superior; Vista inferior; NO CAMBIE LA ESCALA; REVISIÓN; ESCALA:1:2; HOJA 1 DE 1

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

NOMBRE | FIRMA | FECHA | Caracteristicas | TÍTULO: Soporte Eje Reductor NMRV40

DIBUJ. | | | | Detalle A | Profundidad 15mm
VERIF. | | | | Detalle B | Profundidad 2mm
APROB. | | | | Detalle C | Espesor 3mm-4mm

FABR.
CALID. | | | | MATERIAL: Aluminio | N.º DE DIBUJO Pieza 5 | A4

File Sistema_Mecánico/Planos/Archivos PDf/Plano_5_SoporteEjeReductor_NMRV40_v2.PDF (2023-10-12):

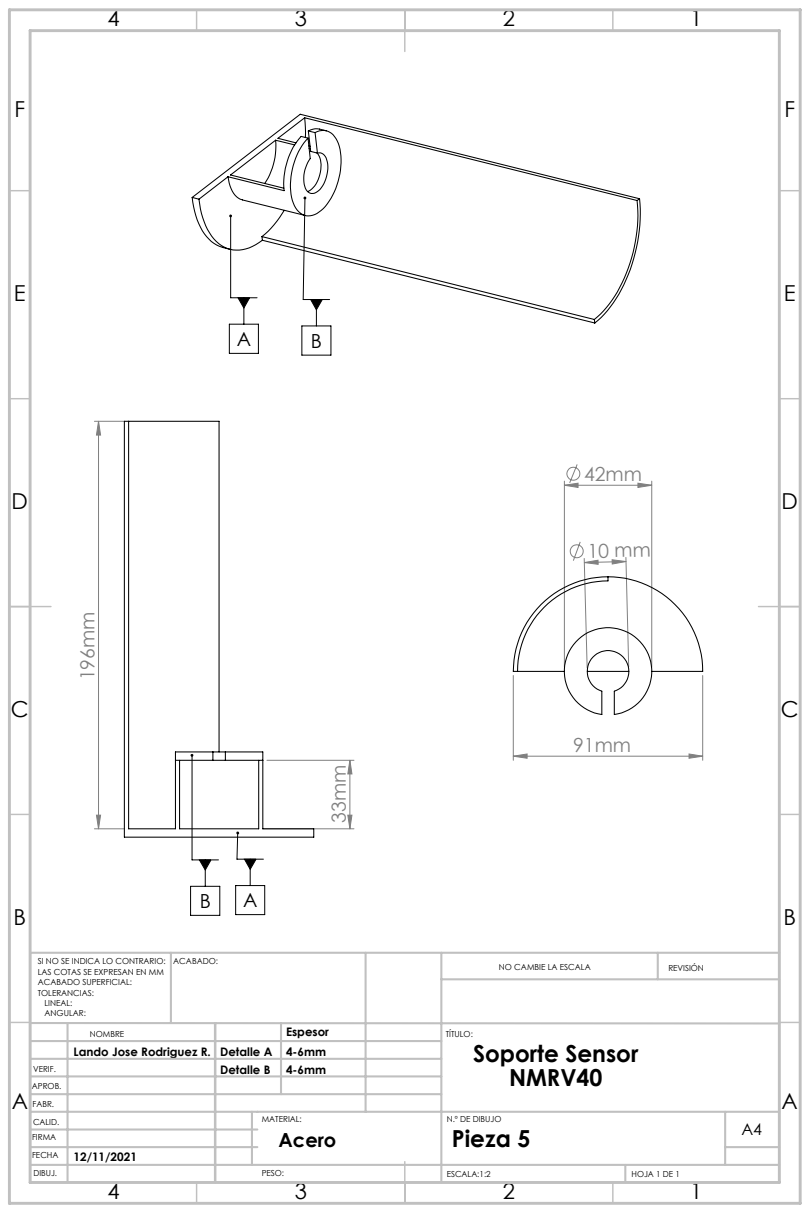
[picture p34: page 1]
NO CAMBIE LA ESCALA; REVISIÓN

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

NOMBRE | | Espesor | | TÍTULO: Soporte Sensor NMRV40
Lando Jose Rodriguez R. | Detalle A | 4-6mm

VERIF. | | Detalle B | 4-6mm
APROB.
FABR.
CALID. | | | MATERIAL: Acero | N.º DE DIBUJO Pieza 5 | A4
FIRMA
FECHA | 12/11/2021
DIBUJ. | | PESO: | | ESCALA:1:2 | HOJA 1 DE 1

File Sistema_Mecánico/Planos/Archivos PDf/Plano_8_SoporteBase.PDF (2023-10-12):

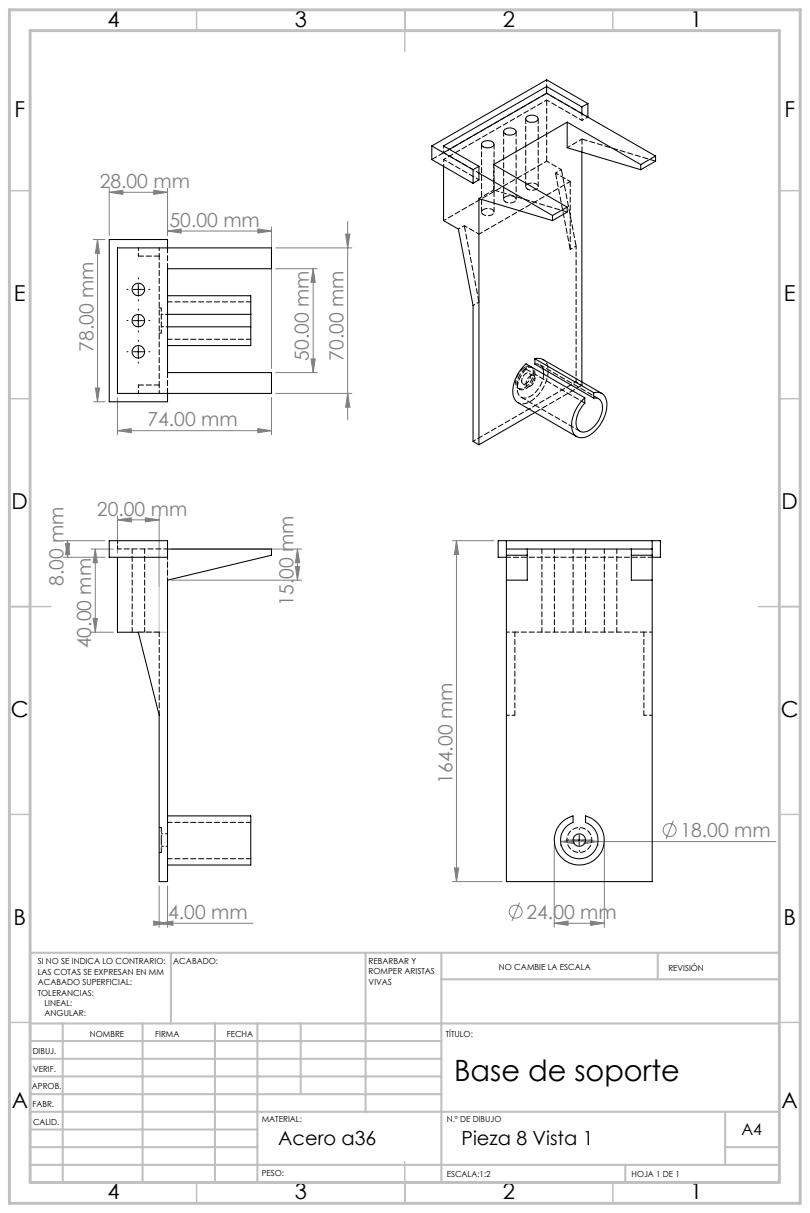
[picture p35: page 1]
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

NOMBRE | FIRMA | FECHA | | | | TÍTULO: Base de soporte

DIBUJ.
VERIF.
APROB.
FABR.
CALID. | | | | MATERIAL: Acero a36 | N.º DE DIBUJO Pieza 8 Vista 1 | A4

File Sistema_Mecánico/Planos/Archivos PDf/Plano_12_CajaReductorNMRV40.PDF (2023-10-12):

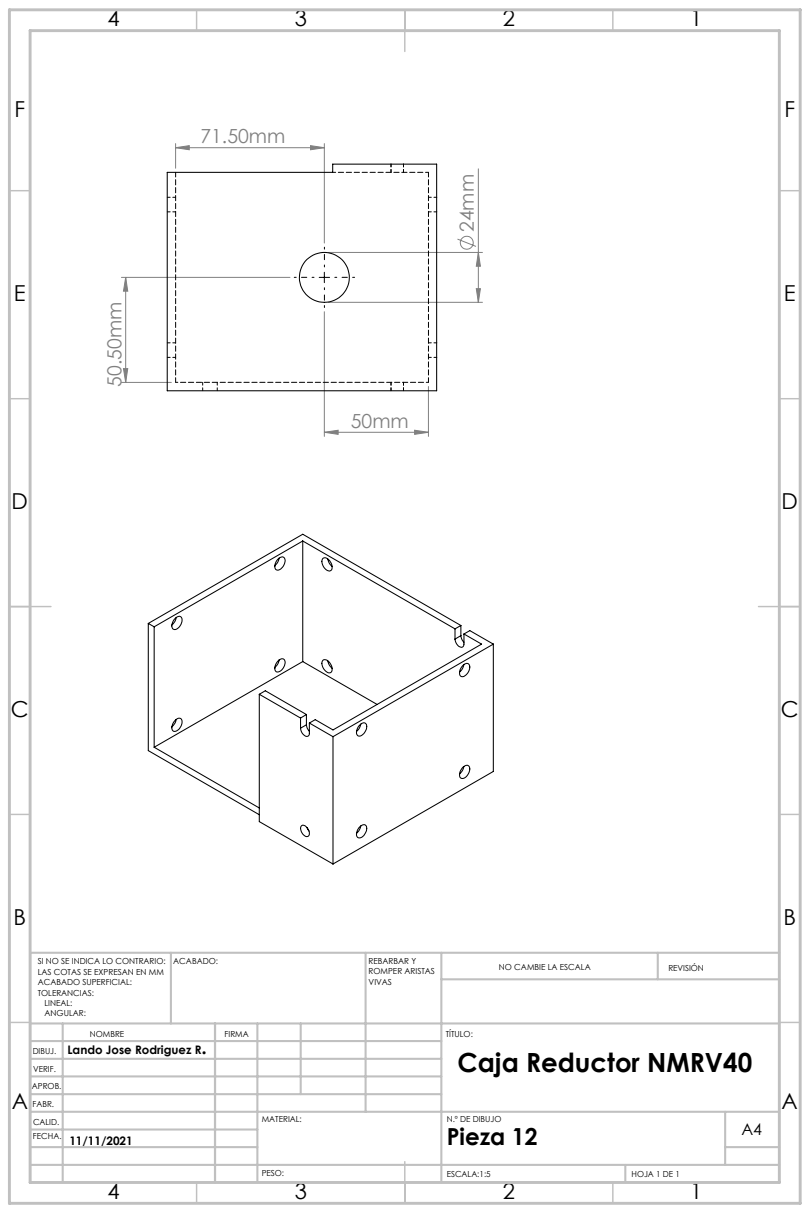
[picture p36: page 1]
ACABADO:; REBARBAR Y; ROMPER ARISTAS; NO CAMBIE LA ESCALA; REVISIÓN; ESCALA:1:5; HOJA 1 DE 1

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

DIBUJ. | Lando Jose Rodriguez R.

NOMBRE | FIRMA | | | | TÍTULO: Caja Reductor NMRV40

VERIF.
APROB.
FABR.
CALID. | | | MATERIAL: | N.º DE DIBUJO Pieza 12 | A4
FECHA. | 11/11/2021

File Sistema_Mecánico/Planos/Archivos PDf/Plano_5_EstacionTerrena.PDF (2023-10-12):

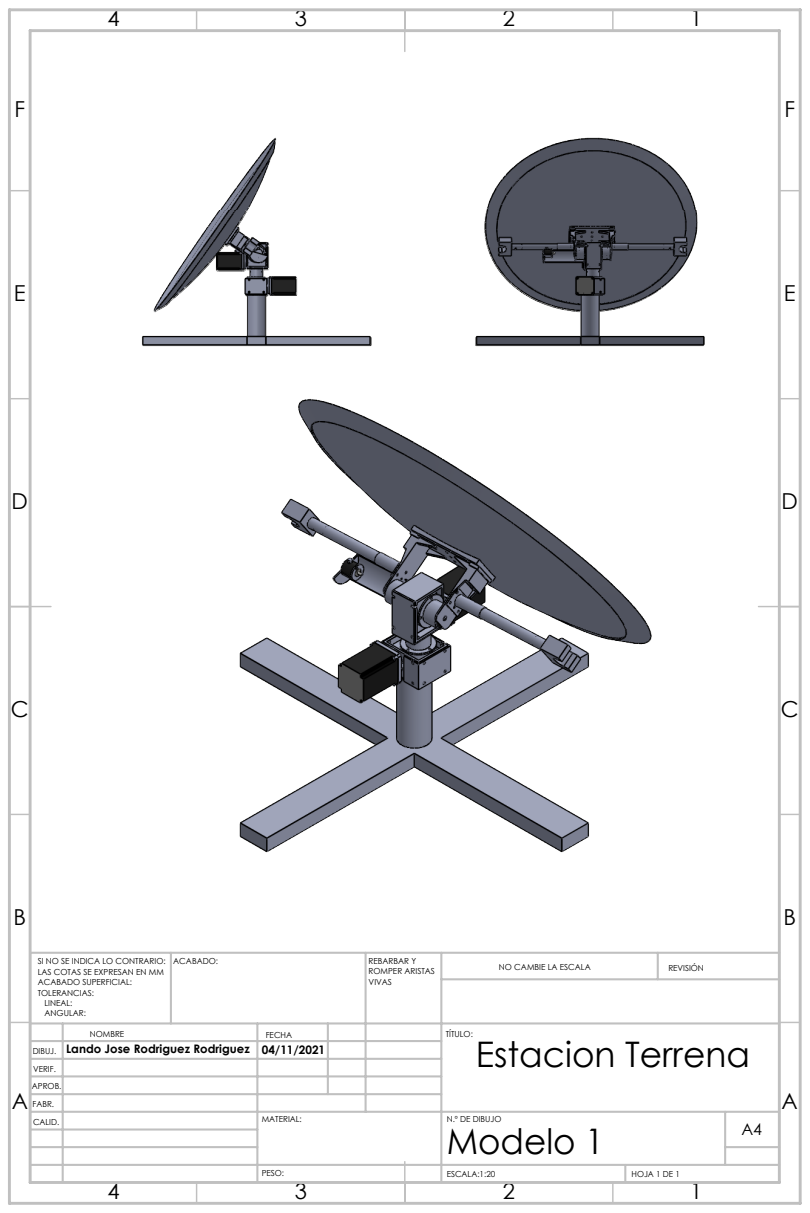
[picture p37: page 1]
ACABADO:; REBARBAR Y; ROMPER ARISTAS; NO CAMBIE LA ESCALA; REVISIÓN; ESCALA:1:20; HOJA 1 DE 1

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

DIBUJ. | | 04/11/2021 | | | Estacion Terrena Lando Jose Rodriguez Rodriguez

NOMBRE | FECHA | | | TÍTULO:

VERIF.
APROB.
FABR.
CALID. | | MATERIAL: | N.º DE DIBUJO Modelo 1 | A4

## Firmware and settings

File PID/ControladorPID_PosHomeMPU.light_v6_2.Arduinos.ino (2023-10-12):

/*________________________________________________
Código PID sensores  de retroalimentacion HMC5883 MPU6050 con Pantalla LCD
Sensores de retroalimentacion HMC5883 | MPU6050
    Posición inicio (home) agregado 

         Librería MPU6050_light
  Hecho por: Alonso Damian Muñoz Rico ICE
    Trabajando correctamente 15/10/22
__________________________________________________*/
#include <Separador.h> //Librería anexa
//#include <MPU6050_tockn.h>  //incluye librería MPU6050

#include <MPU6050_light.h> //incluye librería MPU6050
#include <MechaQMC5883.h> // incluye libreria para magnetometro QMC5883L
#include <Wire.h> //Inicializa comunicacion I2C
#include <EEPROM.h>
//#include <LiquidCrystal_I2C.h> //Pantalla LC D
#include <Tone.h>
#include <PID_v1.h>

int notes[] = { NOTE_A4,
                NOTE_B4,
                NOTE_C4,
                NOTE_D4,
                NOTE_E4,
                NOTE_F4,
                NOTE_G4 };
//LiquidCrystal_I2C lcd(0x27,20,4); //Direccion y pines de salida LCD


//MPU6050 mpu6050(Wire); //Se inicializa la conexion I2C para el sensor MPU6050_knock
MPU6050 mpu1(Wire); //Se inicializa la conexion I2C para el sensor MPU6050_light
MPU6050 mpu2(Wire); //Se inicializa la conexion I2C para el sensor MPU6050_light

unsigned long timer = 0;

//String inputString = "";
//bool stringComplete = false; 
bool home_pos=false;
String azimuthTemp = ""; //Crea una variable temporal donde se guarda el valor del Azimut para la conversion a valor numérico
String elevationTemp = ""; //Crea una variable temporal donde se guarda el valor del Elevación para la conversion a valor numérico
float azimuth ; //Se inicializa el valor de az leido en 0
float elevation ;
//float azimuth; //Se inicializa el valor de az
//float elevation;
int eeAddress=0;
float geografico=0;



Separador s; //Crea un objeto de la clase Separador
MechaQMC5883 qmc;   // crea objeto

#define PUL 7 //Pin para la señal de pulso motor 1
#define DIR 6 //define Direction pin motor 1
#define EN 9 //define Enable Pin motor 1
#define PUL2 5 //Pin para la señal de pulso motor 2
#define DIR2 4 //define Direction pin motor 2
#define EN2 12 //define Enable Pin motor 2

//Variables auxiliares
float posicionAz = 0;
float posicionInicialAz = 0;
float posicionEl = 0;
float posicionInicialEl = 0;
float hist_I[10]={0,0,0,0,0,0,0,0,0,0};
float hist_I2[10]={0,0,0,0,0,0,0,0,0,0};
//Variables para el uso de potenciometro como método de posicionamiento
//int valPot1;
//float angPot1 = 0; 
//int valPot2;
//float angPot2 = 0; //Variables para el uso de Potenciometros

float angHMC = 0;
float angMPU = 0;
int period = 50; //Refresh rate period of the loop is 50ms
float last_z,z;
String inputString = "";         // a String to hold incoming data
bool stringComplete = false;  // whether the string is complete

bool ret=false;
float theta=1|0;
float rho=0;

//float errorPosicion1Prev, errorPosicion1;
//float errorPosicion2Prev, errorPosicion2;

//Valores de las constantes del comportamiento del controlador PID
double Setpoint, Input, Output;
double Setpoint2, Input2, Output2;
//Azimuth
double kp=8; // Se queda en 8.9 para un periodo maximo de 64ms 15 8
double ki=0.2; //0.2      0.2
double kd=0.5; //3100    0.5
//Elevación
double kp2=8; // Se queda en 8.9 para un periodo maximo de 64ms 10 8 
double ki2=0.2; //0.2       0.5
double kd2=0.05; //3100    0.005
PID myPID(&Input, &Output, & Setpoint, kp, ki, kd, DIRECT); //az
PID myPID2(&Input2, &Output2, & Setpoint2, kp2, ki2, kd2, DIRECT); //el
//float PID_p, PID_i, PID_d, PID_total; //Variables auxiliares
//float PID_p2, PID_i2, PID_d2, PID_total2; //Variables auxiliares

//El modelo que se utiliza para el control PID es el siguiente:
//PID = (kp*error)+(PID_i+ki*error)+(kd*(error-errorPrevio)/tiempo)

void PHome(); //Declaración de función posición de inicio(home) ET.  
//void PhomeElevacion(); //Declaracion de funcion de regreso para valores negativos satelite

#define I2C_SLAVE_ADDR 0x27
long data = 100;
long response = 0;
Tone notePlayer[2];

void setup() {
//Serial.begin(9600);
Serial.begin(9600);
  mpu1.setAddress(0x68);
  mpu2.setAddress(0x69);
  notePlayer[0].begin(7);
  notePlayer[1].begin(5);

  //PID inicialización
  myPID.SetMode(AUTOMATIC);
  myPID2.SetMode(AUTOMATIC);

  ////////////
   Wire.begin();
// Comenzamos la transmisión al dispositivo 1
    Wire.beginTransmission(1);
    
//// motor de azimut
//pinMode (PUL, OUTPUT); //Define la salida del pulso como salida
pinMode (DIR, OUTPUT); //Define la salida de direccion como salida
pinMode (EN, OUTPUT); //Define la salida de enable como salida

// motor de elevacion
//pinMode (PUL2, OUTPUT);
pinMode (DIR2, OUTPUT);
pinMode (EN2, OUTPUT);


  Serial.println("Calibrando sensores");
  delay(5000);
 
  //geografico=52;
  mpu1.begin();
  mpu2.begin();
  Serial.println("Iniciando Posicion home & PID...");   // inicializa objeto MPU6050 librería light
  Serial.println(F("Calculando offsets gyro, no mover MPU6050..."));
  delay(100);
  
  //mpu.setGyroOffsets(-3.06, 0.79, 0.04);
  mpu1.calcGyroOffsets();
  mpu2.calcGyroOffsets();
  // Esto es para la calibracion
  mpu1.update();
  mpu2.update();
  z=360-mpu2.getAngleZ();
  PHome(); //Llamar función Posiscion home a ejecutar antes 
           //Antes de ejectutar void loop.
                    
  Serial.println("Estacion terrena en posición home correcta"); 

  }
  
void loop() {
  
//  if(!home_pos){
//    if(!ret){
//      if(theta<350){
//        theta+=0.01;  
//      }else if(theta>=350){
//        ret=true;
//      }
//    }else{
//      if(theta>10){
//        theta-=0.1;
//      }else if(theta<=10){
//        ret=false;
//      }
//    }
//    //rho=5+abs(40*sin(0.5*theta));
//    //azimuth=theta;
//    //elevation=rho;
//  }

  
  
  mpu1.update();
  mpu2.update();
  //int x,y,z;      // variables de los 3 ejes
  //float acimut,geografico;  // variables para acimut magnetico y geografico
  //float declinacion = +5.2;    // declinacion desde pagina: http://www.magnetic-declination.com/
  //qmc.read(&x,&y,&z,&acimut);   // lectura de los ejes y acimut magnetico
//
  //geografico = acimut + declinacion;  // acimut geografico como suma del magnetico y declinacion
  EEPROM.get(eeAddress,geografico);
  last_z=z;
  z=360-mpu2.getAngleZ();
  geografico+=z-last_z;
  //geografico=100;
  //EEPROM.put(eeAddress,geografico);
  while(geografico < 0){      // si es un valor negativo
  geografico+=360;// suma 360 y vuelve a asignar a variable
  }  while(geografico>360){
    geografico-=360;
  }
  //geografico=360-geografico;
  //geografico=161;
  EEPROM.put(eeAddress,geografico);
  angHMC = geografico; //Valor calculado 
  
  angMPU = 90-filtro_MPU(); //angulo Y del giroscopio libreria light

if(Serial.available()){
    stringComplete=false;
//dividirString(); 

}

  
  /*Serial.println("");
  Serial.println("-------Trabajando control PID-------");
  Serial.println("");

  
if (Serial.available()) //Verifica si se está obteniendo respuesta de entrada del puerto serial
{
dividirString(); //Divide la cadena en dos variables numéricas de Az y El recibidas mediante Orbitron (Vease manual de Orbitron anexo)
}
*/
//En las siguientes lineas se hace el proceso matemático para el control PID para azimut
//____PID para azimuth______

//---------------------------PID------------------------------//
  //Azimuth 
  azimuth = 20;
  elevation = 50;
  //azimuth = 100;
  //elevation = 85;
  
  Input = angHMC; //retroalimenación MPU AZIMUTH
  Setpoint = azimuth; // el valor al que debe llegar  
  //Setpoint = 90; // valor de preuba 
  myPID.Compute();
  double  f_az = Output;
  //double  f_az = Output*3.18;
  //Serial.print("Frecuencia en azimuth  ");
  //Serial.println(f_az);

//    if(Output >= 255 ){
//      Output = 255;
//    }else if (Output <= 0 ){
//        Output = 0;
//      }
      
//      if(f_az >= 255 ){
//      Output = 255;
//    }else if (f_az <= 0 ){
//        Output = 0;
//      }

  //Elevación
   
  Input2 = angMPU;
  Setpoint2 = elevation; 
  myPID2.Compute();
  double f_el = Output2;
  //double f_el = Output2*5.1;

//  if(Output2 >=255 ){
//      Output2 = 255;
//    }else if (Output2 <= 0 ){
//        Output2 = 0;
//      }

//      if(f_el >= 255 ){
//      Output = 255;
//    }else if (f_el <= 0 ){
//        Output = 0;
//      }

      

  //float error_az = azimuth - angHMC;
  //float error_el = elevation - angMPU;
  
  //float faz = error_az*3.18;
  //float fel = error_El*6.375; 
  
  //Serial.print("Frecuencia en elevación  ");
  //Serial.println(f_el);

//PID ALONSO

//----------------------Movimiento--------------------------------//

//if(angHMC>=8 && angHMC<=12   && (angMPU>=13.5 && angMPU<=15.5)){
  home_pos=false;
//}
if(f_az>=255.0)f_az=255.0;
if(f_el>=255.0)f_el=255.0;
if(azimuth<5.0)azimuth=5.0;
if(azimuth>350.0)azimuth=350.0;
if(elevation<5.0)elevation=5.0;
if(elevation>90.0)elevation=90.0;
if(azimuth<350 && azimuth>10){
//Condicion para Azimut
//--------------------Azimuth------------------------//
  digitalWrite(EN,LOW);
  if(angHMC<azimuth-1){ //Se define una tolerancia de 1 grado -1 grado
    digitalWrite(DIR,LOW); //movimiento sentido horario
    notePlayer[0].play((int)200);
    //notePlayer[0].play((int)f_az);
  }else if(angHMC>azimuth+1){ //+1 grado
    digitalWrite(DIR,HIGH); //movimiento sentido antihorario
    notePlayer[0].play((int)200);
    //notePlayer[0].play((int)f_az);
  }else{
    digitalWrite(EN,HIGH);
    notePlayer[0].stop();
  }
}else{
  digitalWrite(EN,HIGH);
  notePlayer[0].stop();
  
}
//tone(PUL,400);
//tone(PUL2,400);

//Condicion para elevación

//--------------------Elevación------------------------//

if(elevation<=90 && elevation>-1){
//Condicion para Azimut
//--------------------Elevació------------------------//
  digitalWrite(EN2,LOW);
  if(angMPU<elevation-1 ){ //Se define una tolerancia de 1 grado -1
    digitalWrite(DIR2,LOW); //movimiento sentido horario
    notePlayer[1].play((int)200);
    //notePlayer[1].play((int)f_el);
  }else if(angMPU>elevation+1){ //+1 
    digitalWrite(DIR2,HIGH); //movimiento sentido antihorario
    notePlayer[1].play((int)200);
    //notePlayer[1].play((int)f_el);
  }else{
    digitalWrite(EN2,HIGH);
    notePlayer[1].stop();
  }
}else{
  digitalWrite(EN2,HIGH);
  notePlayer[1].stop();
}
    
    

//Serial.print("Targets: ");
//Serial.print("[AZ]: ");
//Serial.print(azimuth);
//Serial.print(" [EL]: ");
//Serial.print(elevation);
//Serial.print("  Current : ");
//Serial.print("[AZ]: ");
Serial.print(angHMC);
Serial.print(",");
//Serial.print(z);
//Serial.print(",");
//Serial.print(" [EL]: ");
Serial.print(angMPU);
Serial.print(",");
float error_az = azimuth - angHMC;
float error_el = elevation - angMPU;
//Serial.print("   [AZ]: ");
Serial.print(error_az);
Serial.print(",");
Serial.print(millis());
Serial.print(",");
//Serial.print(" [EL]: ");
Serial.print(error_el);
Serial.print(",");
Serial.print(millis());
Serial.print(",");
Serial.print(Output);
Serial.print(",");
Serial.print(Output2);
Serial.print(",");
Serial.print(f_az);
Serial.print(",");
Serial.println(f_el);

//Serial.println();


}

void dividirString(){
if(!home_pos){  
  String datosSerial = Serial.readString(); //Lee los datos del puerto serial
  azimuthTemp = s.separa(datosSerial,',',0); //Utiliza la librería Separador y asigna el primer elemento separado con una coma al azimut
  elevationTemp = s.separa(datosSerial,',',1); //Utiliza la librería Separador y asigna el segundo elemento a la elevación
  //Transforma la cadena a dato numérico para ser tratado en el proceso
  azimuth = azimuthTemp.toFloat();
  elevation = elevationTemp.toFloat();
  if(azimuth<5.0)azimuth=5.0;
if(azimuth>355.0)azimuth=355.0;
if(elevation<5.0)elevation=5.0;
//if(elevation>60.0)elevation=60.0;
}else{
  azimuth=10;
  elevation=25;
}
stringComplete=true;
  if(azimuth<5.0)azimuth=5.0;
if(azimuth>355.0)azimuth=355.0;
if(elevation<5.0)elevation=5.0;
if(elevation>60.0)elevation=60.0;
}
//Ejecuta función home
void PHome(){
  home_pos=true;
  azimuth=10;
  elevation=15.5;

}
  //Función para llamar sensor HMC5883 a ejectutar 
 
//void serialEvent(){
  //stringComplete=false;
//dividirString(); 

//}
float filtro_MPU(){
  float sum=0;
  for(int i=0; i<20;i++){
    mpu1.update();
    sum+=mpu1.getAngleY();
  }
  return sum/20;
}
